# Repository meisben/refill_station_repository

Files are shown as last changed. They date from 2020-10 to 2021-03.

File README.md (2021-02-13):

#  Refill station repository 

This is a repository which contains information for assembly and testing of a refill station prototype

## Contents

* Overview of the refill station
* Repository structure
* Prerequisties

## Overview of the refill station

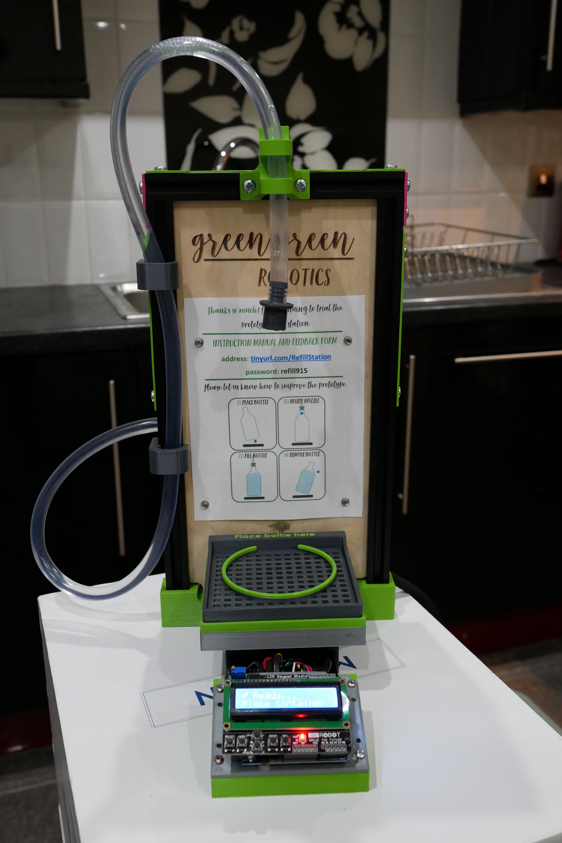
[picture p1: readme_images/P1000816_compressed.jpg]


The refill station is a low cost machine which is used to fill containers with fluid. It is inteded for use in a zero waste store or distributor. In these type of stores fluids are often slow and messy to refill because of their viscocity. The refill station solves this problem.

The operating principle of the refill station is simple, it uses a diaphragm pump controlled by the user to move fluid from a bulk container into a smaller refill container (as shown in the images below).

| Prototype Front | Prototype Back | Working Principle |
| --- | --- | --- |
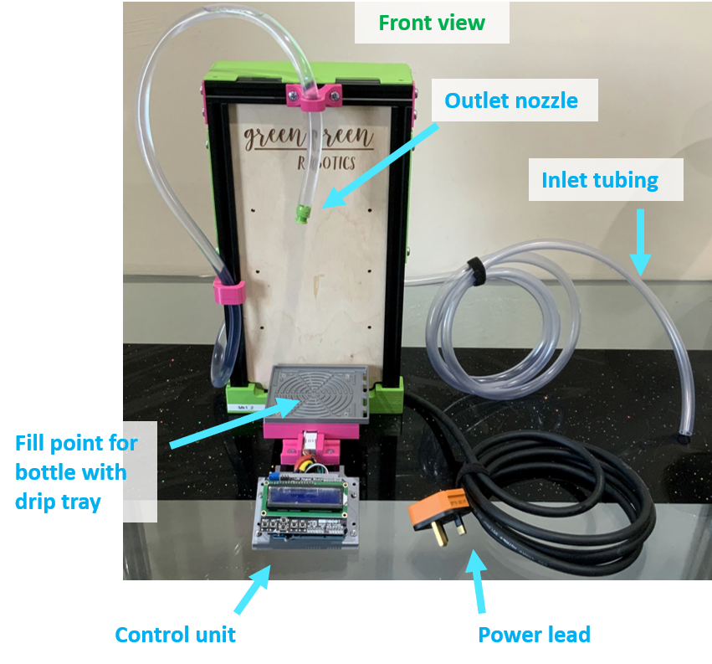
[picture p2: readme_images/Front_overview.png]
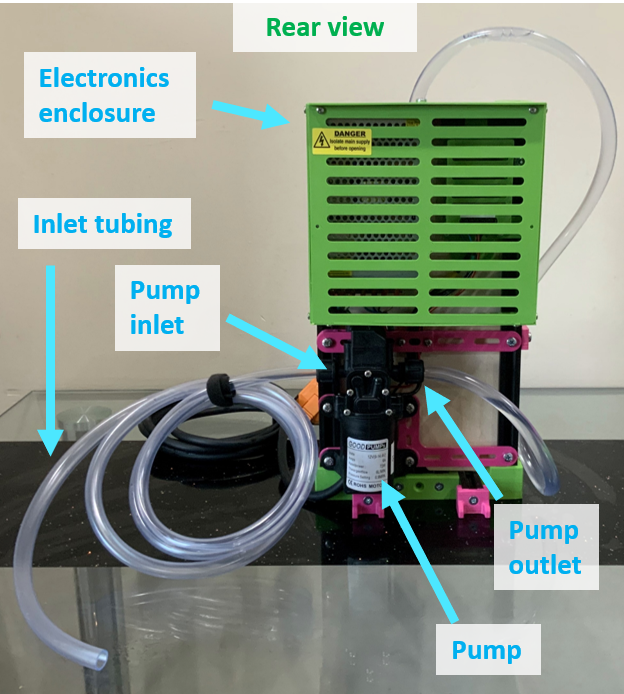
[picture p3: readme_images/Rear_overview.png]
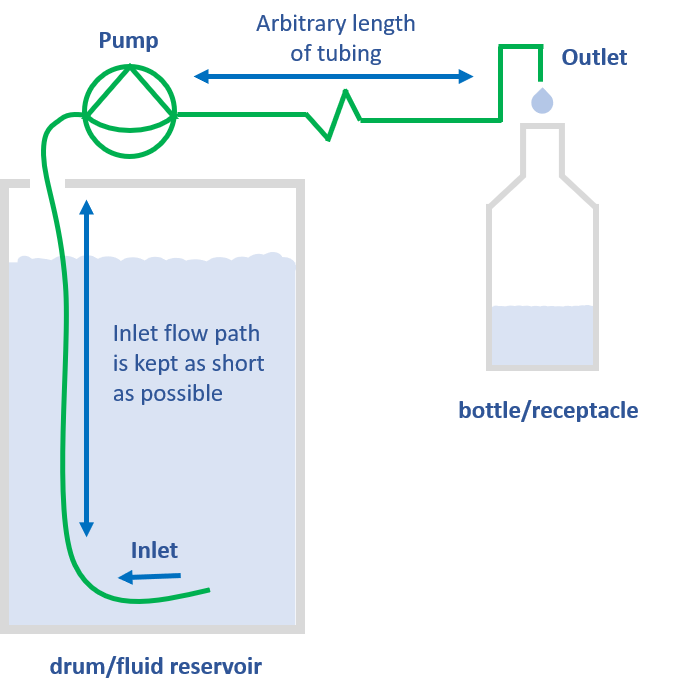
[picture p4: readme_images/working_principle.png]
|  |  |  |

### More information

General information on the refill station prototypes can be found on Green Green Robotics [main website](www.greengreenrobotics.com)

More information on how the refill station is operated can be found at this [weblink](https://meisben.github.io/refill_station_multimedia_supplement/) using the password: refill915

### Variants of the refill station prototoypes

Here high level details are listed on the prototypes which have created and tested / or are under development.

| Unique name | Purpose | Microcontroller type |
| :---: | :---: | :---: |
| MK0 | Proof of concept of pump, and load cell (pump and load cell) | Arduino |
| MK1 | First prototype to be tested with FILL refill (pump and load cell)  | Arduino |
| MK2 | Second prototype to be tested with FILL refill (pump and load cell) | Arduino |
|  MK3_basic  | First prototype for testing in refill stores  (pump only) |  Raspberry Pi Pico |

## Repository structure
The repository has the following structure

| Folder name | Contents | Comment |
| :---: | :---: | :---: |
| assembly_info | Assembly instructions | Note: Not yet fully complete |
| debug_folder | Used to store debug logs | N/A |
| design | Information on the design | N/A |
| production_code | Code used for the refill stations in a 'production' environment | N/A |
| readme_images | Images for Readme | N/A |
| record_of_production | Record of attributes for each completed refill station | N/A |
| testing | Testing instructions | N/A |

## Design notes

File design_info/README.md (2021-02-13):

# Design

This folder contains design information for each version of the refill station prototypes

## Folder contents

| Folder name | Contents | Comment |
| :---: | :---: | :-----: |
| (Prototype UID) | Design information for eachvarient of the refill station. Details are in readme's within each folder. | N/A |
| images | Images for Readme | N/A |

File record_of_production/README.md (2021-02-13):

# Record

This folder contains a record of how each prototype is manufactured and which parts are used

## Folder contents

Currently an excel spreadsheet is used to record this information

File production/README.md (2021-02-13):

# Production code

This folder contains the production code and associated information for the refill station

## Folder contents

| Folder name | Contents | Comment |
| :---: | :---: | :-----: |
| production_code | Code for each production varient of the refill station. Details are in readme's within each folder. You should use the | N/A |
| images | Images for Readme | N/A |

## Software packs used for each prototype

| Unique name | Software Pack Used | Microcontroller type |
| :---: | :---: | :---: |
| MK0 | variantA | Arduino |
| MK1 | variantB | Arduino |
| MK2 | variantC | Arduino |
|  MK3_basic  | variantD |  Raspberry Pi Pico |

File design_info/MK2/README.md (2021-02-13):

# Design - MK2 prototype

This folder contains design information for the MK2 prototype

## Folder contents

| Folder name | Contents | Comment |
| :---: | :---: | :---: |
| CAD | uncontrolled CAD model (in STEP format) | Can be opened with any CAD suite |
| components  | list of components, sourcing information and costs | MS excel file |
| electronics | details on PCB layout and wiring | Can be opened with Fritzing (open source) |

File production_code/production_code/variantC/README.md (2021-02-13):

# Variant C Production Code

## Production code details
Follow the instructions in the table below

This version of the code reads prototype specific settings (HX711 scale factor, custom mass set points) from the EEPROM on the arduino

| Refill Station Type | Production code assignment | Latest Version | Tested? |  Bug list  |
| :---: | --- | :---: | :-----: | :---: |
| Mk2 | variantC14_production_refill_station | vC_14.5.0 | Yes | None known |

## Prerequisites
The following arduino libraries are required to be installed on your system for the full code to work

| Library | Tested version | Authors | URL |
| :---: | :---: | :---: | :---: |
| Liquid Crystal | v1.07 | Hans-Christoph Steiner | [Link](https://github.com/arduino-libraries/LiquidCrystal) |
| HX711 Arduino Library | v0.74 | Bogdan Necula, Andreas Motl | [Link](https://github.com/bogde/HX711) |
| arduino timer | v2.1.0 | Michael Conteras | [Link](https://github.com/contrem/arduino-timer) |
| MD_UISwitch | v2.1.0 | MajicDesigns | [Link](https://github.com/MajicDesigns/MD_UISwitch) |

[//]: # (This is the right format for a comment)

## Program flow chart
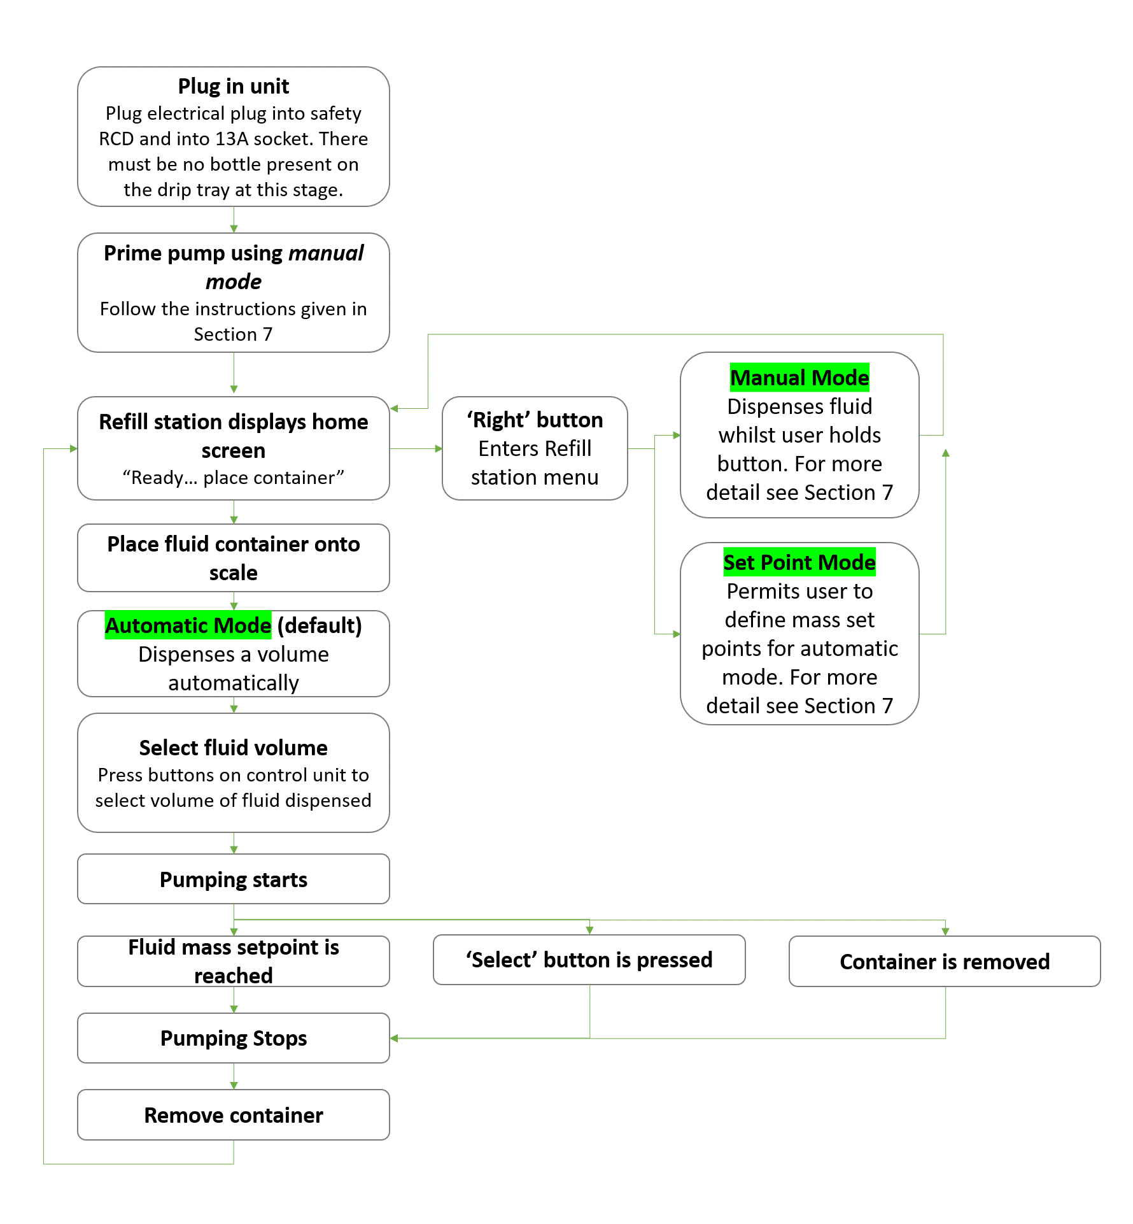
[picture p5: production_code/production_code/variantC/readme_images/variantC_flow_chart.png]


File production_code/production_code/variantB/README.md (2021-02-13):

# Variant B Production Code

## Production code details
Follow the instructions in the table below

### Production code base versions
These are the base 'reference' versions of the code. Updates happen here, are tested on this code, and are manually proliferated to the child versions of the code. Clearly this isn't efficient if the use of this software grows, but it works for prototyping..!

| Refill Station Type | Production code assignment | Latest Version | Tested? |  Bug list  |
| :---: | --- | :---: | :-----: | :---: |
| Mk1 | variantB_production_refill_station | v2.12 | Yes | None known |

## Production code child versions

| Refill Station UID | Production code assignment | Latest Version | Tested? | Scale factor used | Differences from base version |
| :---: | --- | :---: | :-----: | :---: | :---: |
| Mk1_1 | variantB2_production_refill_station | v2.12 | No | 112.157 | [A] Scale factor (for hx711 and strain gauge) [B] "int expectedContainerMass = 50;" (solves creep/drift of scale)  [C] alternate button resitance ladder values |
| Mk1_2 | variantB2_production_refill_station | v2.12 | Yes | 223.61 | No difference |
| Mk1_3 | variantB3_production_refill_station | v2.12 | Yes | 214 | [A] Scale factor (for hx711 and strain gauge) [B] "int expectedContainerMass = 50;" (solves creep/drift of scale) |

## Prerequisites
The following arduino libraries are required to be installed on your system for the full code to work

| Library | Tested version | Authors | URL |
| :---: | :---: | :---: | :---: |
| Liquid Crystal | v1.07 | Hans-Christoph Steiner | [Link](https://github.com/arduino-libraries/LiquidCrystal) |
| HX711 Arduino Library | v0.74 | Bogdan Necula, Andreas Motl | [Link](https://github.com/bogde/HX711) |
| arduino timer | v2.1.0 | Michael Conteras | [Link](https://github.com/contrem/arduino-timer) |
| MD_UISwitch | v2.1.0 | MajicDesigns | [Link](https://github.com/MajicDesigns/MD_UISwitch) |

[//]: # (This is the right format for a comment)

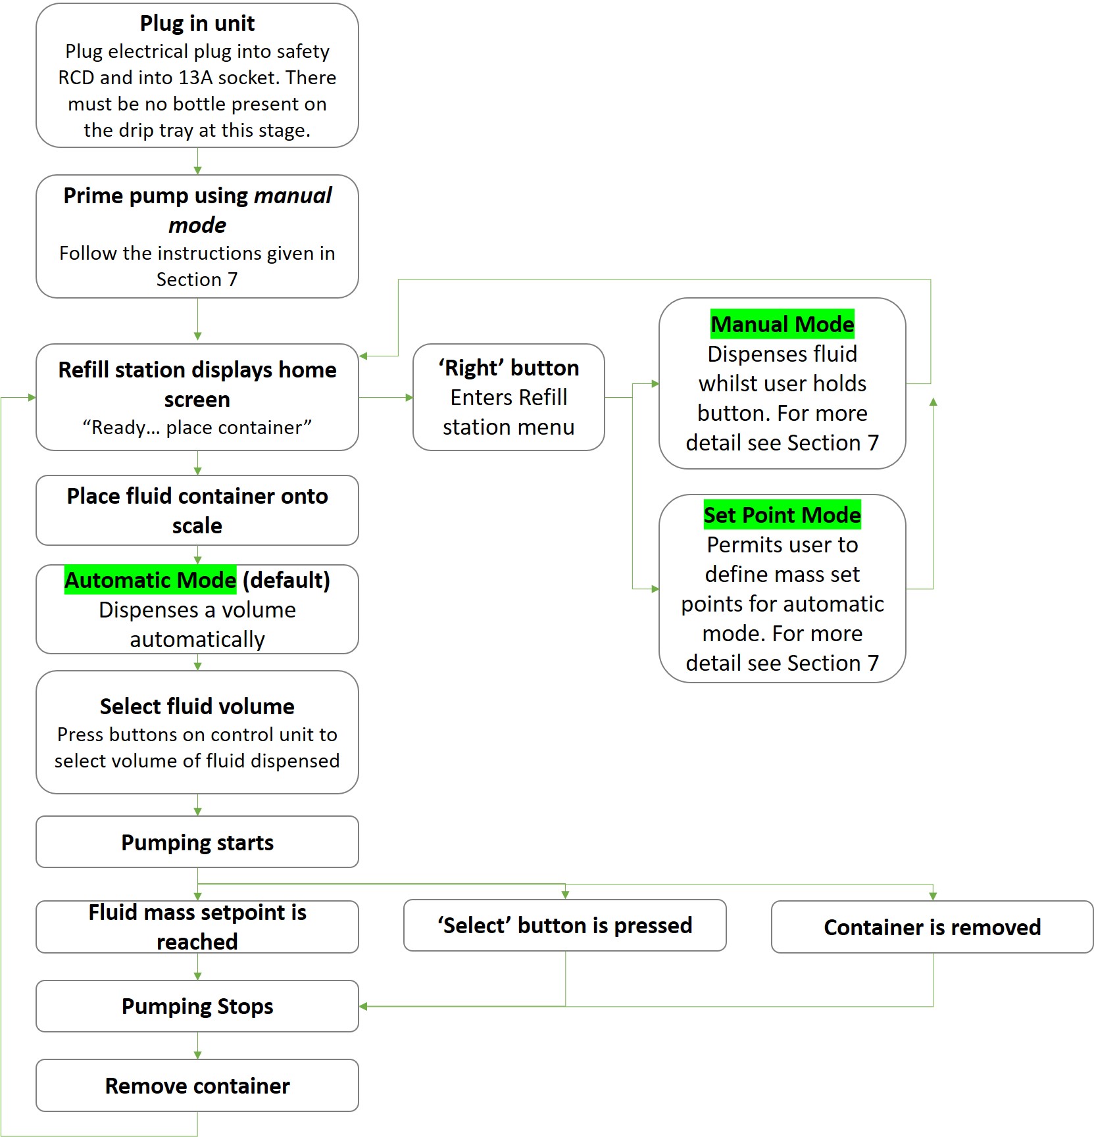
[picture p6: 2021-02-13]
production_code/production_code/variantC/readme_images/variantC_flow_chart.jpg

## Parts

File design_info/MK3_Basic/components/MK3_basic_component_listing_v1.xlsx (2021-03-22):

(Used for ordering)
Quanity | Marked for order | Item | Detail | Used for | Supplier | Supplier P/N | Manufacturer | Manufacturer P/N | Link | Alternative Supplier | Link | Quantity | Units | ROHS compliant? | ROHS detail | FDA approved | Current Quantity in Stock | Units | Cost in (small batch) bulk (inc. Vat) | Per quantity | Units | Cost for each ROHS compliant refill station (inc. Vat) | Anticipated Production cost | Comment
 | N | M5 Pan head screw 6mm | RS PRO, M5 Pan Head, 6mm Steel Pozidriv Bright Zinc Plated | For 2 mm thick pannels | RS components | 908-7693 | RS PRO | 908-7693 | Link (https://uk.rs-online.com/web/p/machine-screws/9087693/) |  |  | 22 | items | Yes | Compliant | N/A |  |  | £4.13 | 100 | items | £0.91 | £0.91
 | N | M5 Pan head screw 12mm | RS PRO, M5 Pan Head, 12mm Steel Pozidriv Bright Zinc Plated | For 7 mm thick pannels | RS components | 553-611 | RS PRO | 553-611 | Link (https://uk.rs-online.com/web/p/machine-screws/0553611/) |  |  | 1 | items | Yes | Compliant | N/A |  |  | £5.38 | 100 | items | £0.05 | £0.05
 | Y | M5 Pan head screw 16mm |  |  |  |  |  |  |  |  |  | 1?
 | N | M5 Countersunk screw 12mm | M5 Countersunk Head, 12mm Steel Pozidriv Bright Zinc Plated | For attaching printed components to tapped aluminium extrusions. For attaching strain gauge mount to aluminium frame. | RS components | 553-469 | RS PRO | 553-469 | Link (https://uk.rs-online.com/web/p/machine-screws/0553469/) |  |  | 12 | items | Yes | Compliant | N/A |  |  | £4.13 | 100 | items | £0.50 | £0.50
 | N | M5 Countersunk screw 20mm |  | For attaching load cell to load cell mount | RS components |  | RS PRO |  |  |  |  | 2 | items | Yes | Compliant | N/A
 | N | M4 Countersunk screw 20 mm |  | For attaching load cell to load cell mount | RS components |  | RS PRO |  |  |  |  | 2 | items | Yes | Compliant | N/A
 | N | M3 Pan Head screw, 6mm | RS PRO, M3 Pan Head, 6mm Steel Pozidriv Bright Zinc Plated |  | RS components | 560-580 | RS PRO | 560-580 | Link (https://uk.rs-online.com/web/p/machine-screws/0560580/) |  |  | 14 | items | Yes | Compliant | N/A |  |  | £2.72 | 100 | items | £0.38 | £0.38
 | N | M3 Countersunk screw, 12 mm |  | For attaching drip tray to support structure | RS components |  | RS PRO |  |  |  |  | 4
 | N | M3 Nut | RS PRO Steel, Hex Nut, M3 |  | RS components | 560-293 | RS PRO | 560-293 | Link (https://uk.rs-online.com/web/p/hex-nuts/0560293/) |  |  | 14 | items | Yes | Compliant | N/A |  |  | £4.73 | 250 | items | £0.26 | £0.26
 | N | PVC flexible tubing | Clear, 13mm OD x 10mm ID | For fluid transfer | RS components | 914-5506 | RS PRO | 914-5506 | Link (https://uk.rs-online.com/web/p/flexible-tubes/9145506/) |  |  | 5 | m | N/A | N/A | Yes | 1 | m | £16.62 | 25 | m | £3.32 | £3.32
 |  |  | Hook up wire | Connecting arduino to electronics board for low power linkages | RS components
 | N | Connecting wire | Higher amperage (6A) wire | Connecting pump motor and power source | RS components | 439-0802 | Nexans | H03VVH2F-2X0.75MM2-NOIR-5 | Link (https://uk.rs-online.com/web/p/electrical-mains-power-cables/4390802/) |  |  | 1 | m | Yes | Compliant | N/A | 1 | m | £27.59 | 25 | m | £1.10 | £1.10
 |  |  | Mains wire
 | N | Plug | 13A fused Permaplug | Mains connection | Screwfix | 38744 | Permaplug | Permaplug |  |  |  | 1 | items |  |  |  | 0 | items | £1.51 | 1 | items | £1.51 | £1.51
 | N | Load cell (10 kg) | Load Cell - 10kg, Straight Bar (TAL220) | Measuring mass of bottle | Mouser | 474-SEN-13329 | SparkFun | SEN-13329 | Link (https://www.mouser.co.uk/ProductDetail/SparkFun/SEN-13329?qs=WyAARYrbSnZgHAzG5X6AUQ==) | Sparkfun (or google TAL220 for ali express) | Link (https://www.sparkfun.com/products/13329) | 1 | items | Yes | Compliant | N/A | 0 | items | £6.95 | 1 | items | £6.95 | £3.00 | When sourced from ali express
 | N | hx711 board |  | Conditioning strain gauge signal | Mouser | 474-SEN-13879 | SparkFun | SEN-13879 | Link (https://www.mouser.co.uk/ProductDetail/SparkFun/SEN-13879?qs=wwacUt%252BV97ucrk9vYOp3tw%3D%3D) | (or ali express for hx711) |  | 1 | items | Yes | Compliant | N/A | 3 | items | £7.88 | 1 | items | £7.88 | £2.00 | When sourced from ali express
 | N | LCD keypad shield | DFRobot Accessories LCD Keypad Shield for Arduino | User input | Mouser | 426-DFR0009 | DFRobot | DFR0009 | Link (https://www.mouser.co.uk/ProductDetail/DFRobot/DFR0009?qs=lqAf%2FiVYw9gopeEKQyddjQ%3D%3D) | (or ali express for LCD keypad shield) |  | 1 | items | Yes | Compliant | N/A | 3 | items | £7.84 | 1 | items | £7.84 | £4.00 | When sourced from ali express
 | N | Arduino R3 | Development Boards & Kits - AVR Arduino Uno - R3 SMD | Processing | Mouser | 474-DEV-11224 | SparkFun | DEV-11224 | Link (https://www.mouser.co.uk/ProductDetail/SparkFun/DEV-11224?qs=WyAARYrbSnZVy5ZI7%252B2ULg%3D%3D) | (or ali express) |  | 1 | items | Yes | Compliant | N/A | 2 | items | £22.65 | 1 | items | £22.65 | £4.00 | When sourced from ali express
 | N | Copper wire | Single Core 1mm diameter Copper Wire | Protoboard soldering | RS components | 779-0713 | Block | CUL 100/1,00 | Link (https://uk.rs-online.com/web/p/copper-wire/7790713/) |  |  | 0.3 | m | Yes | Compliant | N/A | 0 | m | £5.28 | 11 | m | £0.14 | £0.14
 | N | Diode | ON Semi 200V 8A, Silicon Junction Diode, 2-Pin TO-220AC BYW29-200G | For electronics board | RS components | 464-277 | ON Semiconductor | BYW29-200G | Link (https://uk.rs-online.com/web/p/rectifier-diodes-schottky-diodes/0464277/) | ON Semi 600V 10A, Silicon Junction Diode, 2-Pin TO-220F FFPF10UA60ST | Link (https://uk.rs-online.com/web/p/rectifier-diodes-schottky-diodes/8070745/) | 1 | items | Yes | Compliant | N/A |  |  | £2.26 | 10 | items | £0.23 | £0.23
 | N | MOSFET | N-Channel MOSFET, 30 A, 60 V, 3-Pin TO-220SIS Toshiba TK30A06N1,S4X(S | For electronics board | RS components | 827-6179 | Toshiba | TK30A06N1,S4X(S | Link (https://uk.rs-online.com/web/p/mosfets/8276179/) |  |  | 1 | items | Yes | Compliant | N/A |  |  | £3.91 | 10 | items | £0.39 | £0.39
 | Y | Heatsink | AAVID Thermalloy Heatsink, 24°C/W, 19 x 20 x 8.8mm, Screw | For transistor heat dissapation | RS components | 712-4257 | AAVID THERMALLOY | ML7G | Link (https://uk.rs-online.com/web/p/heatsinks/7124257/) |  |  | 1 | items | Yes | Compliant | N/A | 4 | items | £0.94 | 5 | items | £0.19 | £0.19
 | N | Resistor
 | Y | PCB Terminals | 5 Way PCB Terminal Strip |  | RS components | 494-8940 | RS PRO | 494-8940 | Link (https://uk.rs-online.com/web/p/pcb-terminal-blocks/4948940/) |  |  | 1 | items | Yes | Compliant | N/A | 4 | items | £2.59 | 5 | items | £0.52 | £0.52
 | N | Proto board | ICB-288, Matrix Board FR1 with 1mm Holes 2.54 x 2.54mm Pitc | For electronics board | RS components | 631-3009 | Sunhayato | ICB-288 | Link (https://uk.rs-online.com/web/p/matrix-boards/6313009/) |  |  | 1 | items | N/A | N/A | N/A | 0 | items | £1.20 | 1 | items | £1.20 | £1.20
 | N | M3 screw nylon
 | N | Stand offs
 | N | Power supply
 | N | Pump
 |  | Aluminium extrusion
 | Above here is components for the MK2 !
 | ------ |  |  |  |  |  |  |  |  |  |  |  |  |  |  |  |  |  |  |  | Total | £56.03 | £23.71
 | Below here are components for the MK3! (Raspberry Pi Pico)
 |  | Raspberry pi pico | Development board |  | Various | Various |  |  | Link (https://thepihut.com/products/raspberry-pi-pico) |  |  | 1 | items | Yes | Compliant | N/A | 0 | items | £3.60 | 1 | items | £3.60 | £3.60
2 | Y | Through hole DC DC converter | XP Power Through Hole Switching Regulator, 3.3V dc Output Voltage, 7 → 28V dc Input Voltage, 1A Output Current | Voltage step down to rpi pico | RS components | 134-6946 | XP Power | TR10S3V3 | Link (https://uk.rs-online.com/web/p/switching-regulators/1346946/) | Murata Power Solutions Inc. OKI-78SR-5/1.5-W36-C | Link (https://uk.rs-online.com/web/p/switching-regulators/7962141/) | 1 | items | Yes | Compliant | N/A | 0 | items | £2.33 | 1 | items | £2.33 | £2.33
 |  | Female headers for rpi pico | 2.54mm SIL Socket | Removable rpi pico (DIL profile IC) | RS components | 161-3624 | HARWIN | D01-9972042 | Link (https://uk.rs-online.com/web/p/sil-sockets/1613624/) |  |  | 2 | items | Yes | Compliant | N/A | 0 | items | £0.30 | 1 | items | £0.60 | £0.60
 |  | N-channel 3.3V logic MOSFET TO-220 package | ST N-channel 100V - 0.028Ω - 40A TO-220 Low gate charge STripFET™ Power MOSFET | Switching pump on | RS components | 486-2290 | ST | STP40NF10L | Link (https://uk.rs-online.com/web/p/mosfets/4862290/) |  |  | 1 | items | Yes | Compliant | N/A | 0 | items | £0.50 | 1 | items | £0.50 | £0.50
 |  | Resistor (100 Ohm)
 |  | Resistor (10 KOhm)
20 | Y | Decoupling ceramic capacitor (330 nF) | Radial 330nF Multilayer Ceramic Capacitor MLCC 50V dc Through Hole | (1) Capacitance across motor terminals (2) capacitance for raspberry pi pico | RS components | 194-0544 | TDK | FG28X7R1H334KRT00 | Link (https://uk.rs-online.com/web/p/mlccs-multilayer-ceramic-capacitors/1940544/) |  |  | 4 | items | Yes | Compliant | N/A | 0 | items | £0.17 | 1 | items | £0.69 | £0.69
 |  | Smoothing electrolytic capacitor (100 uF) | RS PRO 220μF Electrolytic Capacitor 25V dc, Through Hole | capacitance for raspberry pi pico | RS components | 711-1097 | RS PRO | 711-1097 | Link (https://uk.rs-online.com/web/p/aluminium-capacitors/7111097/) |  |  | 1 | items | Yes | Compliant | N/A | 0 | items | £0.06 | 1 | items | £0.06 | £0.06
 |  | Diode | ON Semi 200V 8A, Silicon Junction Diode, 2-Pin TO-220AC BYW29-200G | For electronics board | RS components | 464-277 | ON Semiconductor | BYW29-200G | Link (https://uk.rs-online.com/web/p/rectifier-diodes-schottky-diodes/0464277/) | ON Semi 600V 10A, Silicon Junction Diode, 2-Pin TO-220F FFPF10UA60ST | Link (https://uk.rs-online.com/web/p/rectifier-diodes-schottky-diodes/8070745/) | 1 | items | Yes | Compliant | N/A | 0 | items | £0.22 | 10 | items | £0.02 | £0.02
 |  | Potentiometer | POT 50K OHM 1/20W LINEAR | For speed control | Digi-Key | P3P5503-ND | Panasonic | EVU-E2AF25B54 | Link (https://www.digikey.co.uk/product-detail/en/panasonic-electronic-components/EVU-E2AF25B54/P3P5503-ND/243655) |  |  | 1 | items | Yes | Compliant | N/A | 0 | items | £0.51 | 1 | items | £0.51 | £0.51
 |  | Fuse | RS PRO 1.5A Axial FF Non-Resettable Wire Ended Fuse, 125V ac/dcRS PRO 1.5A Axial FF Non-Resettable Wire Ended Fuse, 125V ac/dc | Circuit protection (Raspberry pi) | RS components | 764-9472 | RS PRO | 764-9472 | Link (https://uk.rs-online.com/web/p/non-resettable-wire-ended-fuses/7649472/) |  |  | 1 | items | Yes | Compliant | N/A | 0 | items | £0.09 | 1 | items | £0.09 | £0.09
 |  | Plastic stand offs M3 | RS PRO Nylon Hex Standoff Male/Female, 6mm, M3 x M3 | PCB mounting | RS components | 382-967 | RS PRO | 382-967 | Link (https://uk.rs-online.com/web/p/standoffs/0382967/) |  |  | 4 | items | Yes | Compliant | N/A | 0 | items | £0.23 | 1 | items | £0.90 | £0.90
 |  | Plastic screws M3 | Wurth Elektronik, M3 Pan Head, 4mm Nylon Cross | PCB mounting | RS components | 185-4384 | urth Elektronik | 97790403111 | Link (https://uk.rs-online.com/web/p/machine-screws/1854384/) |  |  | 4 | items | Yes | Compliant | N/A | 0 | items | £0.18 | 1 | items | £0.74 | £0.74
 |  | Plastic Nuts M3 | RS PRO Nylon Hex Nut, Plain, M3 | PCB mounting | RS components | 525-701 | RS PRO | 525-701 | Link (https://uk.rs-online.com/web/p/hex-nuts/0525701/) |  |  | 4 | items | Yes | Compliant | N/A | 0 | items | £4.81 | 50 | items | £0.38 | £0.38
 |  | Panel button | RS PRO Double Pole Double Throw (DPDT) Momentary Blue LED Push Button Switch, IP65, 22.2 (Dia.)mm, Panel Mount, 250V ac | On/Off pump | RS components | 175-8967 | RS PRO | 175-8967 | Link (https://uk.rs-online.com/web/p/push-button-switches/1759042/) | RS PRO 175-9049 | Link (https://uk.rs-online.com/web/p/push-button-switches/1759049/) | 1 | items | Yes | Compliant | N/A | 0 | items | £2.87 | 1 | items | £2.77 | £2.77
 |  | Alternative potentiometer (1 of)
 |  | Low value resistor for led | For calc see: https://www.evilmadscientist.com/2012/resistors-for-leds/ | Remember to add the wire resistance based on length and csa
 |  | Connector so that the system can interface with a simple printer
 | Above here are components for the MK3! (Raspberry Pi Pico)
 | ------
 | Below here are additional components for the 555 pwm circuit electronics
100 | Y | Diode (for 555 circuit) | ON Semi 100V 300mA, Diode, 2-Pin DO-35 1N4148-T26A | Diode for 555 circuit | RS components | 186-7593 | ON Semiconductor | 1N4148-T26A | Link (https://uk.rs-online.com/web/p/schottky-diodes-rectifiers/1867593/) |  |  | 2 | items | Yes | Compliant | N/A | 0 | items | £0.01 | 1 | items | £0.03 | £0.03
50 | Y | 555 timer | Texas Instruments NE555P, Timer Circuit, 8-Pin PDIP | 555 timer for PWM | RS components | 221-5535 | Texas Instruments | NE555P | Link (https://uk.rs-online.com/web/p/timer-circuits/2215535/) |  |  | 1 | items | Yes | Compliant | N/A | 0 | items | £0.21 | 1 | items | £0.21 | £0.21
20 | Y | Capacitor (1nF) | EPCOS 1nF Polyester Capacitor PET 200 V ac, 400 V dc ±10%, Through Hole | Timing capacitor for 555 timer | RS components | 194-3479 | EPCOS | B32529C6102K000 | Link (https://uk.rs-online.com/web/p/polyester-film-capacitors/1943479/) | RS components | Link (https://uk.rs-online.com/web/p/polyester-film-capacitors/1854997/) | 1 | items | Yes | Compliant | N/A | 0 | items | £0.08 | 1 | items | £0.08 | £0.08
20 | Y | Capacitor (100nF) | EPCOS 100nF Polyester Capacitor PET 40 V ac, 63 V dc ±5%, Through Hole | Capacitor for 555 voltage smoothing | RS components | 334-221 | EPCOS |  | Link (https://uk.rs-online.com/web/p/polyester-film-capacitors/0334221/) | RS components | Link (https://uk.rs-online.com/web/p/polyester-film-capacitors/4631765/) | 1 | items | Yes | Compliant | N/A | 0 | items | £0.11 | 1 | items | £0.11 | £0.11
 | Have already | Resistor (1K)
 | Y | Resistor (100 ohm) | Vishay 100Ω Metal Film Resistor 0.4W ±5% SFR2500001000JA500 | Resistor for motor transistor | RS components | 165-0763 | Vishay | SFR2500001000JA500 | Link (https://uk.rs-online.com/web/p/polyester-film-capacitors/0334221/)
 |  | Selection of resistors (check which ones you haven't got!)
 |  | To order
 | Y | M5 x 6 countersunk machine screws
 | Y | M4 x 40 countersunk machine screws
 |  | 555 circuit components
 | Y | Female power supply connectors

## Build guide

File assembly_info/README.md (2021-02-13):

# Assembly

This folder contains assembly instructions for the prototype, and code that is used during assembly.

## Folder contents

| Folder name | Contents | Comment |
| :---: | :---: | :---: |
| assembly_instructions | Assembly guide | Please note, this is a work in progress! |
| utlility_programs | code that is used during assembly | (for example to set the scale factor for the HX711, or to write factory settings to the EEPROM) |

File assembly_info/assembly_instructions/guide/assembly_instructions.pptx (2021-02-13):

## Assembly instructions

Refill station
(Version control through github)

## Please note this guide is a work in progress. It isn’t complete!

## Soldering hookup wires to arduino

- Wire length for all hookup wires = 200mm

## Joining hookup wires to main frame wires

- Main frame wire length
  - For Arduino power cable = 450mm
  - For transistor pin = 580mm

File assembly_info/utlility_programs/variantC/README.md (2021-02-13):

# Utility programs (software pack: variant C)

This is code that is used during assembly.

## Folder contents

| Script name | Purpose | Comment |
| :---: | :---: | :-----: |
| eeprom_write_refill_station | initialise EEPROM settings (custom mass set points) | N/A |
| load_cell_with_hx711_calibrate_and_eeprom_write | determine HX711 scale factor and write it to EEPROM | N/A |

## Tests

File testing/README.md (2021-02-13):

# Testing of the assembly and sub assemblies

This folder contains the testing information for the refill station. The prototype is tested during assembly to check each subassembly is functioning correctly (e.g. load cell, PCB, control unit)

## Folder contents

| Folder name | Contents | Comment |
| :---: | :---: | :-----: |
|  test_code  | Testing code for each software pack | N/A |
| images | Images for Readme | N/A |

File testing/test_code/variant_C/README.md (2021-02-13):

# Testing of the assembly and sub assemblies (Software pack: VariantC)

This folder contains the testing information for the refill station MK2 using software pack: Variant C and the arduino development board.

## Test equipment required

| Test equipment name | Consists of | Comment |
| :---: | :---: | :-----: |
| LED tester | 1 x mini breadboard, 1 x LED, 1 x resistor(TBC ohms) | N/A |

## Test method
Follow the instructions in the table below

| Test ID | What is tested? | Associated test code | Version | Stage | Condition | Test steps | Pass criteria |
| :-----: | --- | :---: | --- | ---: | --- | --- | --- |
| Test A1 | Arduino board | Example blink code (from arduino IDE) | N/A | After wiring to arduino | N/A | Execute code | Built in LED flashes |
| Test B1 | Hook up wires: (a) on pin 12, (b) matching ground | pin_test_external_LED.ino | v2.0 | After wiring to arduino | Pin #12 hookup wires are connected to LED tester | Execute code | LED tester flashes |
| Test C1 | Hook up wires: for arduino power source (a) live, (b) matching ground | pin_test_external_LED.ino | v2.0 | After wiring to arduino | Pin #12 hookup wires are connected to LED tester | Execute code | LED tester flashes |
| Test D1 | (a) HX711, (b) strain gauage assembly | strain_gauge_raw_test_hx711.ino | v1.1 | After asembling hx711 and strain gauge | hx711 and strain gauage should be connected and wired into frame. LCD screen can be connected | Execute code | Raw readings are distinct for each weight (TBC) |
| Test E1 | LED shield and its buttons | monitor_button_resitive_ladder_a2d_input.ino | v1.0 | Anytime | LCD Keypad shield is tested | Execute code | Record values on serial monitor |
| Test E2 | LED shield and its buttons | push_button_to_activate_output.ino | v4.1 | After testing steps above | Pin #12 hookup wires are connected to LED tester. Check button resitive ladder values are correct in code (using Test E1 script) | Execute code | LED tester flashes |
| Test F1 | Custom PCB for pump [Test_1] | push_button_to_activate_output.ino | v4.1 | PCB is assembled and mounted onto frame | (a) Pin #12 hookup wires are connected to PCB, and (b) PCB has external power from battery, and (c) PCB output is connected to LED tester | Execute code | LED tester flashes corresponding with button press |
| Test F2 | Custom PCB for pump [Test_2] | push_button_to_activate_output.ino | v4.1 | PCB is assembled and mounted onto frame | (a) Pin #12 hookup wires are connected to PCB, and (b) PCB has external power from power supply, and (c) PCB output is connected to LED tester | Execute code | LED tester flashes corresponding with button press |
| Test F3 | Custom PCB for pump [Test_3] | push_button_to_activate_output.ino | v4.1 | PCB is assembled and mounted onto frame | (a) Pin #12 hookup wires are connected to PCB, and (b) PCB has external power from power supply, and (c) PCB output is connected to pump | Execute code | Pump runs corresponding with button press |
| Test G1 | Calibration of strain gauge | hx711_calibration_script.ino | v1.2 | Full assembly is ready | Test masses (liquid 250ml, 500ml, 1L) are prepared | Execute code and note results in spreadsheet | Note calibration factor, press 'U' for this to be automatically calculated on the arduino |
| Test G2 | Check of strain gauge calibration | hx711_calibration_script.ino | v1.2 | Full assembly is ready | Test masses (liquid 250ml, 500ml, 1L) are prepared | Execute code and check results vs actual weights used ((a) press 'U' on keypad to automatically calculate the scaling fator in Test G1, then press 'D' on keypad) | Masses should be approximately the same! |
| Test H1 | Test of full assembly | Assembly specific (production_code in main folder) | N/A | Full assembly is ready and labelled with UID | Calibration factor and button values are entered into code to be uploaded, and ID of assembly is noted in code | Execute code with water as test fluid | Code runs smoothly with no bugs |

## Prerequisites
All arduino libraries must be installed as per instructions in the main readme (root of this repository)

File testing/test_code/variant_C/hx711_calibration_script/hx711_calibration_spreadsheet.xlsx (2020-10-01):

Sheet: Calibration Factor
Calibration Spreadsheet for hz711 loadcell
Using arduino sketch 'hx711_calibration_script_v1.0'
For the 20kg load cell from ebay |  |  | For the TAL220 straight bar load cell (UID: 01, attached to MK1_2) |  |  | For the TAL220 straight bar load cell (UID: 02, attached to MK1_3)
Known mass (g) | RawResult (ADC reading) | Average Scaling Factor | Known mass (g) | RawResult (ADC reading) | Average Scaling Factor | Known mass (g) | RawResult (ADC reading) | Average Scaling Factor
150 | 16772 | 112.1566667 | 150 | 33877.66667 | 223.6107407 | 150 | 28851.33333 | 212.6955556
300 | 33769 |  | 300 | 66450.66667 |  | 300 | 63273.66667
450 | 50400 |  | 450 | 100921.3333 |  | 450 | 99301
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

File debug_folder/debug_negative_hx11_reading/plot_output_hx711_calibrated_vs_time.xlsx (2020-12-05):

Plot of output vs time
 | t (s) | hx711 value (grams)
 | 0.3 | 282.46
 | 0.6 | 303.66
 | 0.9 | 314.63
 | 1.2 | 327.16
 | 1.5 | 339.76
 | 1.8 | 345.69
 | 2.1 | 358.18
 | 2.4 | 370.31
 | 2.7 | 379.65
 | 3 | 401.99
 | 3.3 | 411.6
 | 3.6 | 424.45
 | 3.9 | 433.95
 | 4.2 | 449.61
 | 4.5 | 455.82
 | 4.8 | 465.55
 | 5.1 | 478.35
 | 5.4 | 487.74
 | 5.7 | 497.5
 | 6 | 510.29
 | 6.3 | 519.95
 | 6.6 | 539.19
 | 6.9 | 545.73
 | 7.2 | 555.61
 | 7.5 | 568.86
 | 7.8 | 578.56
 | 8.1 |  | BAD (approx -372)
 | 8.4 | 600.76
 | 8.7 | 610.28
 | 9 | 626.31
 | 9.3 | 632.63
 | 9.6 | 642.07
 | 9.9 | 654.91
 | 10.2 | 664.32
 | 10.5 | 683.49

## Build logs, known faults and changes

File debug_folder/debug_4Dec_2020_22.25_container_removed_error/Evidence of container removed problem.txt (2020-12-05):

GH filter inactive
Program commencing...
Note: That scale is zeroed during program start up. The scale must have no objects placed on it at startup.
ScalingFactor value (from EEPROM): 1588.48
Reading mass set-point value for:  250ml 
 Which has value(g) of: 180
Reading mass set-point value for:  500ml 
 Which has value(g) of: 400
Reading mass set-point value for: 1000ml 
 Which has value(g) of: 487

Now place fluid receptacle and then press 'right' to start pumping

Scale value (g): -0.07
Scale value (g): -0.09
Scale value (g): -0.02
Scale value (g): -0.00
Scale value (g): -0.07
Scale value (g): -0.05
Scale value (g): 0.03
Select volume to pump using up, down buttons. Then press right key
Scale value (g): 300.86
Scale value (g): 256.11
Scale value (g): 255.66
Scale value (g): 255.13
Scale value (g): 255.31
Scale value (g): 255.33
Scale value (g): 255.25
Scale value (g): 255.24
Check nozzle is inserted in receptacle, confirm with right key
Scale value (g): 255.09
Scale value (g): 255.11
Scale value (g): 254.75
Scale value (g): 254.83
Scale value (g): 254.92
Scale value (g): 255.09
Scale value (g): 254.74
Scale value (g): 254.70
pumpFluidVolume activated with volume, mass =  500ml , 400 g
Container mass recorded as =255 g
Total mass to pump =655 g
Pumping started
Scale value (g): 255.20
filter/scale output myCurrentMass = 256.17
filter/scale output myCurrentMass = 258.34
filter/scale output myCurrentMass = 265.63
filter/scale output myCurrentMass = 272.72
Scale value (g): 275.84
filter/scale output myCurrentMass = 278.87
filter/scale output myCurrentMass = 282.15
filter/scale output myCurrentMass = 285.54
filter/scale output myCurrentMass = 288.59
filter/scale output myCurrentMass = 291.84
Scale value (g): 295.37
filter/scale output myCurrentMass = 298.61
filter/scale output myCurrentMass = 308.18
filter/scale output myCurrentMass = 311.40
Scale value (g): -390.68
filter/scale output myCurrentMass = 314.56
filter/scale output myCurrentMass = 317.97
filter/scale output myCurrentMass = 321.20
filter/scale output myCurrentMass = 324.30
filter/scale output myCurrentMass = 333.94
Scale value (g): 337.06
filter/scale output myCurrentMass = 340.26
filter/scale output myCurrentMass = 343.58
filter/scale output myCurrentMass = 346.90
filter/scale output myCurrentMass = 350.04
filter/scale output myCurrentMass = 353.26
Scale value (g): 356.45
filter/scale output myCurrentMass = 359.74
filter/scale output myCurrentMass = 369.45
filter/scale output myCurrentMass = 372.84
Scale value (g): -390.68
filter/scale output myCurrentMass = 375.84
filter/scale output myCurrentMass = 378.99
filter/scale output myCurrentMass = 382.25
filter/scale output myCurrentMass = 385.54
filter/scale output myCurrentMass = 395.22
Scale value (g): 398.49
filter/scale output myCurrentMass = 401.90
filter/scale output myCurrentMass = 405.10
filter/scale output myCurrentMass = 408.37
filter/scale output myCurrentMass = 411.60
filter/scale output myCurrentMass = 414.78
Scale value (g): 417.86
filter/scale output myCurrentMass = 421.07
filter/scale output myCurrentMass = 431.04
filter/scale output myCurrentMass = 434.10
Scale value (g): 437.24
filter/scale output myCurrentMass = 440.60
filter/scale output myCurrentMass = 443.82
filter/scale output myCurrentMass = -390.68
filter/scale output myCurrentMass = 447.21
Container removed, cancelling pumping!
filter/scale output myCurrentMass = 453.87
Cancel button pressed
Pumping stopped
Scale value (g): 456.83
Scale value (g): 460.28
Select volume to pump using up, down buttons. Then press right key
Scale value (g): 459.37
Scale value (g): 459.17
Scale value (g): 459.08
Scale value (g): 459.29
Scale value (g): 459.10
Scale value (g): 458.98
Scale value (g): 458.91

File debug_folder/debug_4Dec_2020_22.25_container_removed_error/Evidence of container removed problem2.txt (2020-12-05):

Conclusion: the scale error value is -18, and so it's the averaging of two readings which is causing this problem. But by the same logic, I should constantly keep track of a 'currentZero' in state 1, and when a container is placed and pumping starts, all of the error checking can be relative to this 'current zero' which may take account of soap residue in the drip tray.

--Log below---

Scale value (g): -0.04
GH filter inactive
Program commencing...
Note: That scale is zeroed during program start up. The scale must have no objects placed on it at startup.
ScalingFactor value (from EEPROM): 1588.48
Reading mass set-point value for:  250ml 
 Which has value(g) of: 180
Reading mass set-point value for:  500ml 
 Which has value(g) of: 400
Reading mass set-point value for: 1000ml 
 Which has value(g) of: 487

Now place fluid receptacle and then press 'right' to start pumping

Scale value (g): -0.02
  No container present, mass is: -0.23
Scale value (g): -0.02
Scale value (g): -0.22
  No container present, mass is: 0.08
Scale value (g): -0.09
  No container present, mass is: 0.01
Scale value (g): -0.01
Scale value (g): 0.12
  No container present, mass is: -0.06
Scale value (g): 0.13
  No container present, mass is: -0.16
Scale value (g): -0.18
Scale value (g): 10.16
Select volume to pump using up, down buttons. Then press right key
Scale value (g): 345.09
Scale value (g): 286.36
Scale value (g): 283.41
Scale value (g): 281.41
Scale value (g): 281.58
Scale value (g): 281.76
Scale value (g): 281.87
Scale value (g): 281.76
Scale value (g): 280.83
Scale value (g): 280.69
Scale value (g): 280.69
Scale value (g): 281.18
Scale value (g): 280.54
Check nozzle is inserted in receptacle, confirm with right key
Scale value (g): 280.43
pumpFluidVolume activated with volume, mass =  500ml , 400 g
Container mass recorded as =280 g
Total mass to pump =680 g
Pumping started
Scale value (g): 281.75
filter/scale output myCurrentMass = 283.51
filter/scale output myCurrentMass = 285.39
filter/scale output myCurrentMass = -390.87
filter/scale output myCurrentMass = 296.67
Scale value (g): 299.29
filter/scale output myCurrentMass = 302.89
filter/scale output myCurrentMass = 305.88
filter/scale output myCurrentMass = 308.85
filter/scale output myCurrentMass = 311.86
filter/scale output myCurrentMass = 315.25
Scale value (g): -390.87
filter/scale output myCurrentMass = -390.87
filter/scale output myCurrentMass = 324.65
filter/scale output myCurrentMass = 328.05
filter/scale output myCurrentMass = 331.04
filter/scale output myCurrentMass = 334.07
Scale value (g): 337.40
filter/scale output myCurrentMass = 340.44
filter/scale output myCurrentMass = 343.55
filter/scale output myCurrentMass = 346.84
filter/scale output myCurrentMass = 350.07
  No container present, mass is: -18.89
Container removed, cancelling pumping!
filter/scale output myCurrentMass = 356.10
Cancel button pressed
Pumping stopped
Scale value (g): 359.10
Scale value (g): 361.17
Select volume to pump using up, down buttons. Then press right key
Scale value (g): 360.98
Scale value (g): 360.88
Scale value (g): 360.76
Scale value (g): 360.67
Scale value (g): 360.65
Scale value (g): 360.52
Scale value (g): 360.42
Scale value (g): 360.25
Scale value (g): 360.62
Scale value (g): 360.29
Scale value (g): 360.08
Scale value (g): 360.40
Scale value (g): 360.02
Scale value (g): 360.04
Scale value (g): 359.99
Scale value (g): 359.83

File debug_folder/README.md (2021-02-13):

# Debug

This folder contains debug logs for the refill station

## Folder contents

Unorganised debug logs

## Future goals

To organise the debug logs!

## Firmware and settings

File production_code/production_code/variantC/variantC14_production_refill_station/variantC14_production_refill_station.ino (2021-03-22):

/*
   ~~~~~Prerequisites~~~~~

   See Github Readme

   ~~~~~Details~~~~~~~~~~~~

   Authors: Ben Money-Coomes
   Date: 4/1/21
   Purpose: Production code baseline for prototype refill station (version C14). For usage see Github readme
   References: See Github Readme

   ~~~~Version Control~~~~~

   v1.0 - [Checkpoint] This version is working and printing values to the serial monitor
   v1.1 - Working on investigating the functionality of the HX711 loadcell, also printing a value to the LCD
   v1.2 - [Checkpoint] Script to calculate scaling factor for the scale. Will be saved seperately!
   v1.3 - [Checkpoint] Functionality for automatic pumping is working!
   v1.4 - Adding an additional timer to try and get rid of the error where MD_UISwitch sees multiple button presses ... Solved ! ! :)
   v1.41 - Checking on bug where you place a container for the second time, I should just printout two values .... the setPointMass, and the calibratedMassReading ... it's seems like it's not a bug but I added the debug flag with extra printing anway
   v1.42 - Adding function to print to the LCD screen to simplify the code
   v1.43 - Adding text to better describe for the user what to do, adding a state machine function, adding a function to keep track of whether a container is placed ... 98% working ! , I just need to ad actual masses of fluid !
   v1.44 - Squishing cancel button bug.
   v1.45 - [Checkpoint]improve squishing of cancel button bug by moving functionality directly into the button function and making all ouputs low as soon as cancel button is pressed ! Fully working program ! Happy with this for prototype :)
   v1.51 - minor adjustments to timing
   v1.52 - Adding actual fluid masses from measured experimental shampoo results (see spreadsheet). Corrected hardware bug for pin 4 which is shared with LCD keypad. This must be pin 12 or another unused pin.
   v2.00 - [Checkpoint, production]
   v2.10 - Adjusting masses in garden with water to get correct weights
   v2.11 - Adjusting code to variant B -> to accomodate TAL220 strain gauge and D1Robot keypad
   v2.11a - Ajusting to variant B2 (no changes)
   v2.12 - Squishing bug where eroneous button presses after pumping were carried forward to the next bottle (added line "buttonPressActive = false; // reset status to ignore any erroneous button presses and wait for next button press" to case 0 of the state machine)
   v2.12_draftv1 - Looking to implement a low pass filter to see if it improves the pumping variation performance
   v_C_12.3 - [Checkpoint] note: the up button is still problematic
   v_C_12.4 - working on changing button flow
   v_C_12.5 - [Checkpoint] everything is working
   v_C_12.6 - working on writing Mass Set Points to the EEPROM using new states --> all working in v2
   v_C_12.6 - working on removing bug caused by ocassional erroneous big negative HX711 readings
   v_C_12.7 - [Checkpoint] Working version, no major bugs. Need to (1) add compensating factor for pump/fluid intertia, and (2) Periodically prompt user to tare scale if zero drifts
   v_C_12.7 - working on (1) add compensating factor for pump/fluid intertia
   v_C_12.8 - [Checkpoint] Added compensating factor for fluid inertia, but discovered bug with extreme high erroneous value from scale
   v_C_12.9 - working on removing extreme high erroneous value from scale (I think i've sold it), There is also a bug where you zero the scale, when you take it off it says ready to pump -> should enter state where scale needs re-zeroing
   v_C_13.0 - removed tare error from scale (removed by taring it after a 5s delay to allow any power fluctuations to pass)
   v_C_13.1 - working on removing the bug:  where you zero the scale with a bottle on it, when you take it off it says ready to pump -> should enter state where scale needs re-zeroing
   v_C_13.2 - [Checkpoint] Everything is working
   v_C_13.3 - working on adding functionality so that if you hold down a button then things will keep pumping until it is released, I'm probably going to use the 'right' button for this as when pressed the button pin voltage should be around zero. Currently pump pin is changed to LED Pin on line 224!
   v_C_13.4 - This is working ! Just need to add actual pin turn on to manual mode. And then sort out the menu order. State machine has been updated to best practice. Also removing totally the printLCD function will free up a LOT of memory!
   v_C_13.5 - Working on the issues above (printLCD -> removed) (Output pin -> added)
   v_C_13.6 - Working on the issues above 
   v_C_13.7 - [Checkpoint] Everything is working, stable version
   v_C_13.8 - Adding a custom value to the setpoints with title 'Custom' which will have intial value same as 250 ml
   v_C_13.9 - [Checkpoint] Everything is working, stable version
   v_C_14.0 - [Checkpoint] Working on removing bugs, which (1) erroneouly cause menus to be entered into sometimes because 'buttonActive' isn't reset, (2) adjusting fudge factor for setpoint to reduce this by half, (3) the set point mode and manual mode should return to menu if the left button is pressed
   v_C_14.1 - In the above list of issued (2) has been solved. (1) and (3) have also been solved :) ! 
   v_C_14.2 - [Checkpoint] Everything is generally working but the buttons often result in the wrong input, they're a bit of a nightmare. In next version i will be trying to add an if statement with a timer to the button function to resolve this
   v_C_14.3 - as explained in above line. I've implemented this and i'm testing it now
   v_C_14.4 - [Checkpoint] Everything is working and stable, ready to ship to FILL

*/

/* * * * * * * * * * * * * * * * * * * * * * * * * * * * * * * * * * * * * * * * *
   Library Includes.                                                             *
 * * * * * * * * * * * * * * * * * * * * * * * * * * * * * * * * * * * * * * * * */

#include <HX711.h> // for loadcell // https://github.com/bogde/HX711
#include <LiquidCrystal.h> // for LCD screen
#include <MD_UISwitch.h> // for reistor ladder buttons on LCD shield
#include <arduino-timer.h> // to create timers // https://github.com/contrem/arduino-timer
#include "g_h_filter_class.h" // allows filtering of the mass sensor readings
#include <EEPROM.h> // for EEPROM

/* * * * * * * * * * * * * * * * * * * * * * * * * * * * * * * * * * * * * * * * *
  Definitions                                                                    *
 * * * * * * * * * * * * * * * * * * * * * * * * * * * * * * * * * * * * * * * * */
//Start address for EEPROM -----------------
#define  SCALING_FACTOR_START_ADDRESS 0
#define  MASS_SETPOINT_START_ADDRESS  5 //Starting position in the address space

//Timer definitions ------------------------

auto timer = timer_create_default(); // create a timer with default settings

//MD_UISwitch defintions----------------------

const uint8_t ANALOG_SWITCH_PIN = A0;       // switches connected to this pin

// These key values work for most LCD shields
// Can be found using button_test_v1.0.ino script in drafts folder
MD_UISwitch_Analog::uiAnalogKeys_t kt[] =
{
  { 5, 5, 'R' },  // Right
  { 100, 50, 'U' },  // Up
  { 257, 15, 'D' },  // Down
  { 410, 15, 'L' },  // Left
  { 640, 15, 'S' },  // Select
};

//// These key values work for the "D1 Robot" LCD shields (at least one of them!)
//MD_UISwitch_Analog::uiAnalogKeys_t kt[] =
//{
//  { 5, 5, 'R' },  // Right
//  { 131, 20, 'U' },  // Up
//  { 307, 15, 'D' },  // Down
//  { 480, 15, 'L' },  // Left
//  { 720, 15, 'S' },  // Select
//};


// Initialise Switch
MD_UISwitch_Analog pushbuttonSwitch(ANALOG_SWITCH_PIN, kt, ARRAY_SIZE(kt));

// LCD Display -----------------------------
// LCD display definitions
#define  LCD_ROWS  2
#define  LCD_COLS  16

// LCD pin definitions - change to suit your shield
#define  LCD_RS    8
#define  LCD_ENA   9
#define  LCD_D4    4
#define  LCD_D5    LCD_D4+1
#define  LCD_D6    LCD_D4+2
#define  LCD_D7    LCD_D4+3

static LiquidCrystal lcd(LCD_RS, LCD_ENA, LCD_D4, LCD_D5, LCD_D6, LCD_D7);

// HX711 strain gauge -----------------------------
// HX711  definitions
HX711 scale;
//long int values = 0;

// HX711 circuit wiring
const int LOADCELL_DOUT_PIN = 2;
const int LOADCELL_SCK_PIN = 3;

// Note that when using the LCD Keypad Shield then pin 2 is the 3rd pin from the rhs and pin 3 is the 4th pin from the rhs

// G-H filter constants -----------------------------

#define GH_FILTER_ACTIVE 0 // --> 1 if active, 0 if inactive
#define G_CONSTANT 0.6
#define H_CONSTANT 0.2

// Error limit - for scale error catching ----------------------------------
const bool scaleErrorCatching = true; //if true error catching is active and erroneous readings are ignored
#define NEGATIVE_ERROR_LIMIT -50 //readings below this value are considered an error, if the refill station sees a value below this in state 1, then it will prompt the user to reset the scale before continuing
#define SCALE_ZERO_ERROR_TOLLERANCE 15 //readings just above or above this value when the program is in state 0 should be considered an error
#define POSITIVE_ERROR_TOLLERANCE_DURING_PUMPING 500 // readings above this relative number during pumping are considered an error (in the massExceeded function) and ignored. This is because the mass should be increasing approximately linearly. 
#define NEGATIVE_ERROR_TOLLERANCE_DURING_PUMPING -10 //readings below this relative number during this pumping are considered an error (in the massExceeded function) and ignored. This is because the mass should be increasing approximately linearly. A seperate function still checks if the container has been removed
float lastMassValue;

// LCD characters ----------------------------------

const byte up_arrow[8] = {
  B00000,
  B00100,
  B01110,
  B10101,
  B00100,
  B00100,
  B00100,
};

const byte down_arrow[8] = {
  B00000,
  B00100,
  B00100,
  B00100,
  B10101,
  B01110,
  B00100,
};

const byte right_arrow[8] = {
  B00000,
  B00100,
  B00010,
  B11111,
  B00010,
  B00100,
  B00000,
};

const byte left_arrow[8] = {
  B00000,
  B00100,
  B01000,
  B11111,
  B01000,
  B00100,
  B00000,
};

const byte hour_glass[8] = {
  B11111,
  B11111,
  B01110,
  B00100,
  B01110,
  B11111,
  B11111,
};

const byte tick_symbol[8] = {
  B00001,
  B00011,
  B00011,
  B10110,
  B11110,
  B01100,
  B00000,
};

const byte warning_mark[8] = {
  B11111,
  B11011,
  B11011,
  B11011,
  B11111,
  B11011,
  B11111,
};

const byte info_sign[8] = {
  B11111,
  B11011,
  B11111,
  B11011,
  B11011,
  B11011,
  B11111,
};

const byte g_top_left[8] = {
  B11111,
  B11111,
  B11000,
  B11000,
  B11000,
  B11000,
  B11000,
};

const byte g_top_right[8] = {
  B11111,
  B11111,
  B00011,
  B00000,
  B00000,
  B00000,
  B00000,
};

const byte g_bottom_left[8] = {
  B11000,
  B11000,
  B11000,
  B11000,
  B11000,
  B11111,
  B11111,
};

const byte g_bottom_right[8] = {
  B00000,
  B00111,
  B00111,
  B00011,
  B00011,
  B11111,
  B11111,
};

/* * * * * * * * * * * * * * * * * * * * * * * * * * * * * * * * * * * * * * * * *
  Global Variables                                                               *
* * * * * * * * * * * * * * * * * * * * * * * * * * * * * * * * * * * * * * * * */

// For keeping track of the program state
// the possible states of the state-machine
typedef enum { STATE_noContainer,
               STATE_WaitForSelectionCommand,
               STATE_WaitForPumpCommand,
               STATE_AutoPumpingCommandActive,
               STATE_AutoPumpingFinished,
               STATE_MenuTitle,
               STATE_MenuScreen,
               STATE_ManualContainerCheck,
               STATE_ManualPumping,
               STATE_ManualContainerRemovalCheck,
               STATE_SetPointTitle,
               STATE_SetPointDescription,
               STATE_SetPointMenu,
               STATE_SetPointContainerCheck,
               STATE_SetPointRecordContainerMass,
               STATE_SetPointFillCheck,
               STATE_SetPointRecordFluidMass,
               STATE_SetPointContainerRemoval,
               STATE_ErrorContainerRemoved,
             } states;

states currentProgramState = STATE_noContainer;
bool firstTimeInState = false;

// For calibration
float scalingFactor = 1588.48; //note that this is changed by default on startup by reading custom values from the EEPROM (usually set by utility program pre-production) this is a safety value only

// For pumping trigger
const int outputPinPump1 =  12; // The output pin assigned to this pump, note this is normally pin '12', but 'LED_BUILTIN' can be usefully used for debugging! Note that it can't share the same pins as the LCD shield !
//const int outputPinPump1 =  LED_BUILTIN;
bool outputPinPump1_trigger = false; // Used to call the pump trigger
bool outputPinPump1_triggerActive = false;  // Used to confirm record that it has been implemented
bool outputPinPump_emergencyStop = false; // Used to cancel pumping

// For parameters relating to the mode menu
byte modeSelectionIndex = 0; // Used to index the modeSelection arrays, this defines the default (corresponds to manual Mode)

// For storing the text relating to the modes in an array
const char modeText1[] = "Manual mode";
const char modeText2[] = "Set point mode";

const char * modeStrings[] =
{
  modeText1,
  modeText2,
};

// For parameters relating to the manual pumping mode
bool manualPumpingStarted = false;
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
void loop()
{
  readLCDShieldButtons();
  timer.tick();
}


/* * * * * * * * * * * * * * * * * * * * * * * * * * * * * * * * * * * * * * * * *
  Functions                                                                      *
 * * * * * * * * * * * * * * * * * * * * * * * * * * * * * * * * * * * * * * * * */


bool readLCDShieldButtons() {

  buttonState = pushbuttonSwitch.read(); // check button statue

  switch (buttonState)
  {
    //    Note: uncomment for additional functionality!

    //    case MD_UISwitch::KEY_NULL:                                    break;
    //    case MD_UISwitch::KEY_UP:                                      break;
    //    case MD_UISwitch::KEY_DOWN:                                    break;
    case MD_UISwitch::KEY_PRESS:           //Serial.println("KEY_PRESS");

      lastButtonPressed = (char)pushbuttonSwitch.getKey(); //global variable
      switch (lastButtonPressed) // if you need a default button behaviour enter it here
      {
        case 'S': //select button (designated as the emergency stop button)
          emergencyStop();
          //          Serial.println(F("Debug:S pressed"));
          break;
      }
      if(!buttonPressActive){
        bool result = isButtonPressActiveTimerComplete();
        if(result){
          buttonPressActive = true;
        }
      }     
      
      break;
      //    case MD_UISwitch::KEY_DPRESS:    Serial.println("KEY_LONGPRESS"); break;
      //    case MD_UISwitch::KEY_LONGPRESS: Serial.println("KEY_LONGPRESS"); break;
      //    case MD_UISwitch::KEY_RPTPRESS:  Serial.println("KEY_RPTPRESS");  break;
      //    default:                         Serial.println("KEY_UNKNWN");    break;
  }

  return true; // important, to ensure timer continues to repeat this function!
}


// To command the pump to pump a volume of fluid
void pumpFluidVolume(int myMassToPump) {

  containerMass = scale.get_units(3); //the average of x readings from the ADC minus tare weight, divided by the SCALE parameter set with set_scale
  if (debug_verbose) {
    Serial.print(F("Container mass recorded as ="));
    Serial.print(containerMass);
    Serial.println(F(" g"));
  }
  if (containerMass <= 20) {
    Serial.println(F("Error: no container placed on scale"));
  }
  else {
    outputPinPump1_trigger = true;
    massToPump = myMassToPump + containerMass;
    if (debug_verbose) {
      Serial.print(F("Total mass to pump ="));
      Serial.print(massToPump);
      Serial.println(F(" g"));
    }

  }
}

// To manage the trigger start/stop of the pump
bool managePumptriggers() {

  if (outputPinPump1_trigger == true) {

    if (!outputPinPump1_triggerActive) {
      lastMassValue = scale.get_units(3); //initialise this value
      digitalWrite(outputPinPump1, HIGH);
      outputPinPump1_triggerActive = true; // turn the output on
      Serial.println(F("Pumping started"));
      massFilter.reset(scale.get_units(1), 0, 300, G_CONSTANT, H_CONSTANT);
    }
    else {
      bool stopSignal = false;
      float myCurrentMass = scale.get_units(1);
      if (debug_verbose) {
        Serial.print(F("  scale output myCurrentMass = "));
        Serial.println(myCurrentMass);
      }

      // the below if statement is active if the G-H filter is active, and the scale is not returning a erroneous negative reading
      if (GH_FILTER_ACTIVE == 1 && !isScaleReadingErroneousDuringPumping(myCurrentMass, lastMassValue)) {
        float myFilterMass = massFilter.return_value(myCurrentMass);
        if (debug_verbose) {
          Serial.print(F("    filter output myFilterMass = "));
          Serial.println(myFilterMass);
        }
        myCurrentMass = myFilterMass;
      }

      bool stopSignalMassExceeded = false;

      // Check if reading is erroneous, and if not see if the mass has been exceeded
      if (!isScaleReadingErroneousDuringPumping(myCurrentMass, lastMassValue)) {
        stopSignalMassExceeded = isMassExceeded(myCurrentMass, massToPump); // returns true if pumping volume is exceeded
      }

      if (!isScaleReadingErroneousDuringPumping(myCurrentMass, lastMassValue)) {
        lastMassValue = myCurrentMass; //store the mass reading for error checking
      }

      bool stopSignalCancelButton = manageCancelButton(); //returns true if cancel button is pressed
      stopSignal = (stopSignalMassExceeded || stopSignalCancelButton); // stopSignal takes an logical 'OR' value

      if (stopSignal == true) {
        digitalWrite(outputPinPump1, LOW);   // turn the output off
        outputPinPump1_triggerActive = false;
        outputPinPump1_trigger = false;
        Serial.println(F("Pumping stopped"));
      }
    }
  }

  return true; // important, to ensure timer continues to repeat this function!
}

// To check if the mass being pumped has exceeded the set point
bool isMassExceeded(float currentMass, float massToExceed) {
  if (currentMass >= massToExceed) {
    Serial.println(F("Mass exceeded set point"));
    return true;
  }
  else {
    return false;
  }
}

// To enable the cancel button functionality
bool manageCancelButton() {
  if (cancelSignal == true) {
    cancelSignal = false;
    Serial.println(F("Cancel button pressed"));
    return true;
  }
  else {
    return false;
  }
}

// To manage whether a receptacle is detected on the scale and whether it has been removed. Protect against fluid spills. Allow correct text to be shown to user
bool isContainerPresent() {

  float thisCurrentMass = scale.get_units(1); //the average of x readings from the ADC minus tare weight, divided by the SCALE parameter set with set_scale

  if (thisCurrentMass <= expectedContainerMass && !isScaleReadingErroneous(thisCurrentMass)) {
    if (debug_verbose) {
      Serial.print(F("  No container present, mass is: "));
      Serial.println(thisCurrentMass);
    }
    return false;
  }
  else {
    return true;
  }
}

// To manage whether a reading when a container is removed is incorrectly interpreted as a container being placed
bool isContainerRemoved() {
  float thisCurrentMass = scale.get_units(5); //the average of x readings from the ADC minus tare weight, divided by the SCALE parameter set with set_scale
  if (debug_verbose) {
    Serial.print(F("isContainerRemoved mass: "));
    Serial.println(thisCurrentMass);
  }

  if (thisCurrentMass <= (-1 * SCALE_ZERO_ERROR_TOLLERANCE)) {
    return true;
  }
  else {
    return false;
  }

}

bool isScaleReadingErroneous(float myReading) {
  if (scaleErrorCatching) {
    if (myReading < NEGATIVE_ERROR_LIMIT) {
      return true;
    }
    else {
      return false;
    }
  }
  else {
    return false;
  }
}

bool isScaleReadingErroneousDuringPumping(float myReading, float myLastReading) {
  if (scaleErrorCatching) {

    if (myReading < myLastReading + NEGATIVE_ERROR_TOLLERANCE_DURING_PUMPING || myReading > myLastReading + POSITIVE_ERROR_TOLLERANCE_DURING_PUMPING) {
      //      Serial.println("Reading erroneous");
      return true;
    }
    else {
      //      Serial.println("Reading not erroneous");
      return false;
    }
  }
  else {
    //    Serial.println("Reading not erroneous");
    return false;
  }
}

bool isButtonPressActiveTimerComplete(){
  // This function is used to add a timer to the button press sensing function. It has a kind of deboucing effect (hopefully!)
  // when bool bpaTimerStatus is true then the timer is active
  if(!bpaTimerStatus){
    //if the timer is not active, i.e. first call of this function after bool buttonPressActive is set to false
    bpaTimerStartTime = millis();
    bpaTimerStatus = true;
    return false; // return false as the function return value because the timer is not complete
  }
  else{
    //if the timer is active
    bpaTimeNow = millis();
    unsigned long timePassed = abs(bpaTimeNow - bpaTimerStartTime);

    if(timePassed > bpaWaitTime){
      return true; // timer is complete
    }
    else{
      return false; // timer is not complete
    }
    
  }
}

void printScaleValueToSerial() {
  Serial.print(F("Scale value (g): "));
  Serial.println(scale.get_units(1)); //prints to serial constantly for debugging purposes, can be graphed!
}
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

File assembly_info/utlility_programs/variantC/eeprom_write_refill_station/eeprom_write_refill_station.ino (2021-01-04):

/*
   ~~~~~Prerequisites~~~~~

   See Github Readme

   ~~~~~Details~~~~~~~~~~~~

   Authors: Ben Money-Coomes
   Date: 2/12/20
   Purpose: Utility program for saving mass set points (and if desired, scaling factor) to an arduino/microcontroller EEPROM so they can be read for production code
   References: See Github Readme

   ~~~~Version Control~~~~~

   v1.0 - [Checkpoint] This version is working and printing values to the serial monitor and LCD screen
*/

/* * * * * * * * * * * * * * * * * * * * * * * * * * * * * * * * * * * * * * * * *
   Library Includes.                                                             *
 * * * * * * * * * * * * * * * * * * * * * * * * * * * * * * * * * * * * * * * * */

#include <LiquidCrystal.h>
#include <EEPROM.h> // for EEPROM

/* * * * * * * * * * * * * * * * * * * * * * * * * * * * * * * * * * * * * * * * *
  Definitions                                                                    *
 * * * * * * * * * * * * * * * * * * * * * * * * * * * * * * * * * * * * * * * * */

// LCD Display -----------------------------
// LCD display definitions
#define  LCD_ROWS  2
#define  LCD_COLS  16

// LCD pin definitions - change to suit your shield
#define  LCD_RS    8
#define  LCD_ENA   9
#define  LCD_D4    4
#define  LCD_D5    LCD_D4+1
#define  LCD_D6    LCD_D4+2
#define  LCD_D7    LCD_D4+3

static LiquidCrystal lcd(LCD_RS, LCD_ENA, LCD_D4, LCD_D5, LCD_D6, LCD_D7);

// EEPROM ------------------------------------
// Starting position in the address space
#define  SCALING_FACTOR_START_ADDRESS 0
#define  MASS_SETPOINT_START_ADDRESS 5

/* * * * * * * * * * * * * * * * * * * * * * * * * * * * * * * * * * * * * * * * *
  Global Variables                                                               *
* * * * * * * * * * * * * * * * * * * * * * * * * * * * * * * * * * * * * * * * */

// For deciding if scaling factor will be stored
const bool writeScalingFactor = false;
const float scalingFactor = 1588.48; //1588.48 for mk2_varC1

// For storing the values relating to the masses in an array
int massValues[] = {180, 400, 840, 180};

// For storing the text relating to the masses in an array
char massText1[] = " 250ml ";
char massText2[] = " 500ml ";
char massText3[] = "1000ml ";
char massText4[] = "Custom ";

char * massStrings[] =
{
  massText1,
  massText2,
  massText3,
  massText4
};

// Custom LCD screen characters
const byte hour_glass[8] = {
  B11111,
  B11111,
  B01110,
  B00100,
  B01110,
  B11111,
  B11111,
};

const byte tick_symbol[8] = {
  B00001,
  B00011,
  B00011,
  B10110,
  B11110,
  B01100,
  B00000,
};

/* * * * * * * * * * * * * * * * * * * * * * * * * * * * * * * * * * * * * * * * *
  Start of main program                                                          *
* * * * * * * * * * * * * * * * * * * * * * * * * * * * * * * * * * * * * * * * */

void setup() {
  //start serial
  Serial.begin(9600);
  Serial.println(F("Program starting -> writing values to EEPROM"));

  // Set up the LCD ------
  // set up the LCD's number of columns and rows:
  lcd.begin(16, 2);
  lcd.createChar(4, hour_glass);
  lcd.createChar(5, tick_symbol);

  // Write Scaling Factor value if desired
  if(writeScalingFactor){
    lcdPrint("  Writing scale","factor to EEPROM",false);
    lcd.setCursor(0,0);
    lcd.write(byte(4));

    Serial.print(F("Writing scaling factor with value of: "));
    Serial.println(scalingFactor);
    Serial.println(F(""));

    EEPROM.put(SCALING_FACTOR_START_ADDRESS, scalingFactor);
    delay(1000);
  }
   
  // Write EEPROM Values
  lcdPrint("  Writing set-","points to EEPROM",false);
  lcd.setCursor(0,0);
  lcd.write(byte(4));
  delay(1000);

  //Write the mass set points to the EEPROM, each int takes 2 bytes in the address space  
  for (byte i = 0; i < (sizeof(massValues) / sizeof(massValues[0])); i++) {
    Serial.print(F("Writing value of: "));
    Serial.print(massValues[i]);
    Serial.print(F("g for the volume: "));
    Serial.println(massStrings[i]);
    EEPROM.put(MASS_SETPOINT_START_ADDRESS+(2*i), massValues[i]);
  }
  
  //Test read for each position
  Serial.println(F("Reading written values ...")); 
  float temp_float_val;
  int temp_int_val;

  EEPROM.get(SCALING_FACTOR_START_ADDRESS, temp_float_val);
  Serial.print(F("Scaling factor read value: "));
  Serial.println(temp_float_val);
  
  for (byte i = 0; i < (sizeof(massValues) / sizeof(massValues[0])); i++) {
    Serial.print(F("Reading set-point value for: "));
    Serial.println(massStrings[i]);
    
    EEPROM.get(MASS_SETPOINT_START_ADDRESS+(2*i), temp_int_val);
    Serial.print(F(" Which has value(g) of: "));
    Serial.println(temp_int_val);
  }

  //end program
  Serial.println(F("End of program"));
  lcdPrint("  All complete", "Program ended",false);
  lcd.setCursor(0,0);
  lcd.write(byte(5));
}

void loop() {
  // Nothing required to be done in the loop! this program runs once only :) 
}

/* * * * * * * * * * * * * * * * * * * * * * * * * * * * * * * * * * * * * * * * *
  Functions                                                                      *
 * * * * * * * * * * * * * * * * * * * * * * * * * * * * * * * * * * * * * * * * */

 void lcdPrint(char *lcdString1, char *lcdString2, bool autoscrollStatus) {
  lcd.clear();
  if (autoscrollStatus) {
    lcd.autoscroll();
  }
  else {
    lcd.noAutoscroll();
  }

  lcd.setCursor(0, 0);
  lcd.print(lcdString1);
  lcd.setCursor(0, 1);
  lcd.print(lcdString2);
}

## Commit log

2020-09-19 updates for test code
    [hx711_calibration_spreadsheet.xlsx, refill_station_record.xlsx]
2020-10-01 Updates to remove bugs and document code
    [hx711_calibration_spreadsheet.xlsx]
2020-10-01 Updates to squash bug for v2.11 of refill code
    Squash eroneous button press bug
    [variantB_production_refill_station.ino]
2020-10-02 updates to squish button bug (actioned when no receptacle is placed)
    [variantB2_production_refill_station.ino, variantB3_production_refill_station.ino, variantB_production_refill_station.ino]
2020-12-01 Updates for Variant C (working with G-H filter)
    Still issues with the buttons creating a bug, am working on this for the next update
    [variantB1_production_refill_station.ino, variantB1_production_refill_station_draftv1.ino, variantB2_production_refill_station.ino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]
2020-12-05 updates to improve accuracy and debug erroneous scale value
    [Checkpoint] working
    [plot_output_hx711_calibrated_vs_time.xlsx]
2021-01-05 updates to squish bugs
    [variantC1_production_refill_station_update_v12.ino]
2021-01-05 Updates to add timer for button debouncing
2021-02-13 updates for Jie Wei (3)
    [component_listing_v5.xlsx, hx711_calibration_spreadsheet.xlsx, pump_fritzing_layout_v6.fzz]
2021-02-13 updates 13th Feb (4)
    [component_listing_v5.xlsx, hx711_calibration_spreadsheet.xlsx, pump_fritzing_layout_v6.fzz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]
2021-02-13 updates 13th Feb (5)
    [plot_output_hx711_calibrated_vs_time.xlsx]
2021-02-18 updates for MK3_basic
    [MK3_basic_component_listing_v1.xlsx, refill_station_electronics_layout_v1.fzz, temp_refill_station_layout_test_v1.fzz]
